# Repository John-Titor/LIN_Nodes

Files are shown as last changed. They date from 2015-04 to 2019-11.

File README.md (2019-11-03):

Firmware and PCB designs for various LIN network nodes intended for retrofitting older vehicles.

```
boards/
    Eagle schematic and PCB files.

common/
    Protocol definitions and generator.

Documentation/
    Datasheets for various parts used in the design.

lintool
    Host-side configuration tool. Talks to the usb_link hardware.

nodes/
    All of the nodes in this part of the tree are based on the Atmel ATTiny167.

    bl_core/
        LIN bootloader core, consumed by bl_installer.

    bl_installer/
        Bootloader installer; flashed onto a fresh board this will install the
        bootloader.

        The installed bootloader comes up on NAD 32 and can be flashed with lintool
        by explicitly supplying the node address and firmware file.

        lintool update -n 32 <path-to-fw-file>

        Only one node can be in this 'recovery' mode on the network when doing this.

    lib/
        Shared code.

    master/
        Network master node. Supports 7 switch-to-battery and 14 switch-to-ground
        inputs. 4 of the switch-to-ground inputs can also be 0-5V voltage inputs,
        with optional 2 or 16mA current sources for measuring resistive sensors.

    power_v3/
        5-output power switching node using Freescale smart high-side switches.
        Board limited to 5.5A, but code should work with the 10A device as well.
        Outputs support PWM, current monitoring, open- and short-circuit detection,
        overcurrent and overtemperature protection, etc.

    usb_link/
        USB bridge with support for configuration and node firmware updates.

```

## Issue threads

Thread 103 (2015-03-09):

define test hardware configuration

John-Titor, 2015-03-09:
Probably:

 - USB link
 - master connected to Phidget relay board
 - slave connected to Phidget control board, also current & voltage sensor connected
 - 12V power supply on bus

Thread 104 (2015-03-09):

build test framework

John-Titor, 2015-03-09:
Subtask of #29

Framework should support at least:

- Initialise and check for all required hardware
- Utility functions for generating, loading, verifying node configuration
- Utility functions for measuring voltage, current, signal state
- Utility functions for controlling relays
- Complex checking functions (check for blinking, measure duty cycle, capture one-shot behaviours)
- Simple tests for verifying the correct configuration of the test hardware setup
- Logging
- Test runner

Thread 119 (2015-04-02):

param ... -d option does not work as documented

John-Titor, 2015-04-02:
It claims to print the default value, but instead it will cause the value to be set to its default.

Need to work out which is correct...

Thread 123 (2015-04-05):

turn marker lights off after timeout

John-Titor, 2015-04-05:
In order to avoid running the battery down, we should turn off the marker lights after a reasonable period

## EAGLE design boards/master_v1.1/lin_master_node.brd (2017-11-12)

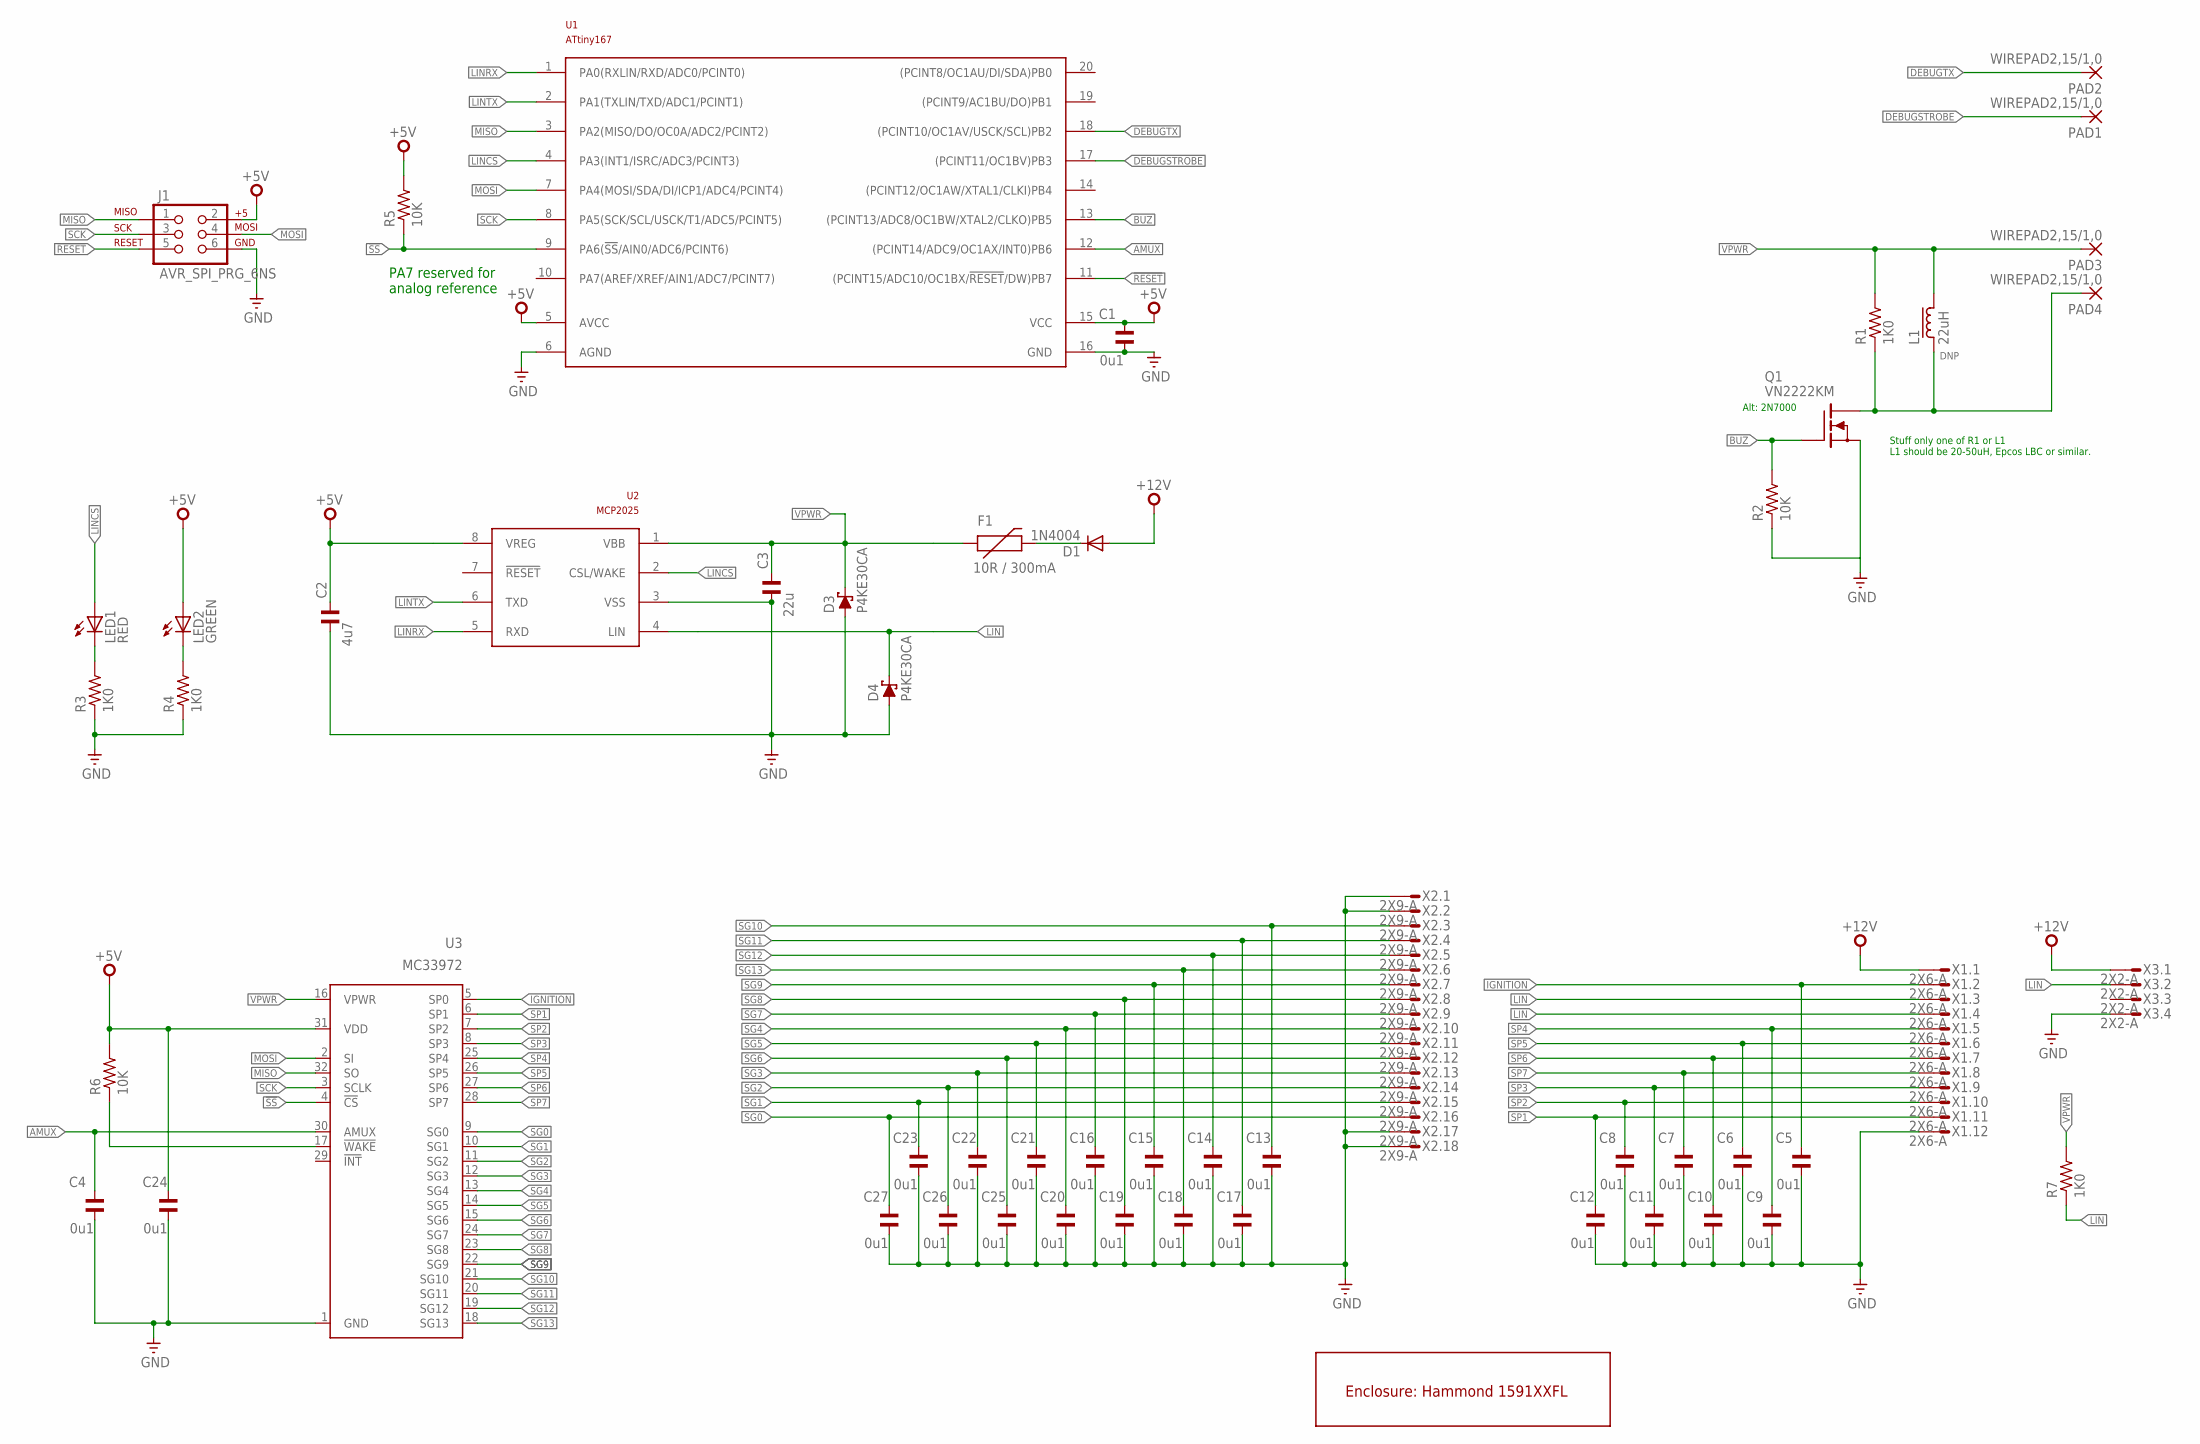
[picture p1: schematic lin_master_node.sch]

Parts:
C1, C4, C24: 0u1; C050-024X044; PARTNO FK28X7R1H104K
C2: 4u7; C050-024X044; PARTNO FK28X5R0J475K
C3: 22u; C050-024X044; PARTNO FK22X5R1E226M
C5, C6, C7, C8, C9, C10, C11, C12, C13, C14, C15, C16, C17, C18, C19, C20, C21, C22, C23, C25, C26, C27: 0u1; C0805K; PARTNO C2012X7R1H104K085AA
D1: 1N4004; DO41-10; PARTNO 1N4004-TP
D3, D4: P4KE30CA; DO41-10; PARTNO P4KE30CA
F1: 10R / 300mA; PTC; PARTNO CMF-RL10-0
J1: AVR_SPI_PRG_6NS; 2X3-NS
L1: 22uH; LBC15A
LED1: RED; LED3MM; PARTNO C4SMF-RJS-CT0W0BB2
LED2: GREEN; LED3MM; PARTNO C4SMF-GJS-CV0Y0792
PAD1, PAD2, PAD3, PAD4: WIREPAD2,15/1,0; 2,15/1,0
Q1: VN2222KM; TO237
R1, R3, R4, R7: 1K0; 0207/10; PARTNO CF14JT1K00
R2, R5, R6: 10K; 0207/10; PARTNO CF14JT10K0
U1: ATtiny167; SO20W; PARTNO ATTINY167-SU
U2: MCP2025; SO08; PARTNO MCP2025-500E/SN
U3: MC33972; SOIC32W; PARTNO MC33972ATEW
U$1: 1591XXAFL; PARTNO 1591XXAFLBK
X1: 2X6-A; 4-794618-2; PARTNO 4-794618-2
X2: 2X9-A; 4-794618-8; PARTNO 4-794618-8
X3: 2X2-A; 3-794618-4; PARTNO 3-794618-4

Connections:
!RESET: J1.5, U1.11 ((PCINT15/ADC10/OC1BX/!RESET!/DW)PB7)
!SS: R5.1, U1.9 (PA6(!SS!/AIN0/ADC6/PCINT6)), U3.4 (!CS)
+5V: C1.1, C2.1, C24.1, J1.2, LED2.A, R5.2, R6.2, U1.5 (AVCC), U1.15 (VCC), U2.8 (VREG), U3.31 (VDD)
+12V: D1.A, X1.1, X3.1
AMUX: C4.1, U1.12 ((PCINT14/ADC9/OC1AX/INT0)PB6), U3.30 (AMUX)
BUZ: Q1.2 (G), R2.2, U1.13 ((PCINT13/ADC8/OC1BW/XTAL2/CLKO)PB5)
DEBUGSTROBE: PAD1.1, U1.17 ((PCINT11/OC1BV)PB3)
DEBUGTX: PAD2.1, U1.18 ((PCINT10/OC1AV/USCK/SCL)PB2)
GND: C1.2, C2.2, C3.2, C4.2, C5.2, C6.2, C7.2, C8.2, C9.2, C10.2, C11.2, C12.2, C13.2, C14.2, C15.2, C16.2, C17.2, C18.2, C19.2, C20.2, C21.2, C22.2, C23.2, C24.2, C25.2, C26.2, C27.2, D3.A, D4.A, J1.6, Q1.3 (S), R2.1, R3.1, R4.1, U1.6 (AGND), U1.16 (GND), U2.3 (VSS), U3.1 (GND), X1.12, X2.1, X2.2, X2.17, X2.18, X3.4
IGNITION: C5.1, U3.5 (SP0), X1.2
LIN: D4.C, R7.1, U2.4 (LIN), X1.3, X1.4, X3.2
LINCS: LED1.A, U1.4 (PA3(INT1/ISRC/ADC3/PCINT3)), U2.2 (CSL/WAKE)
LINRX: U1.1 (PA0(RXLIN/RXD/ADC0/PCINT0)), U2.5 (RXD)
LINTX: U1.2 (PA1(TXLIN/TXD/ADC1/PCINT1)), U2.6 (TXD)
MISO: J1.1, U1.3 (PA2(MISO/DO/OC0A/ADC2/PCINT2)), U3.32 (SO)
MOSI: J1.4, U1.7 (PA4(MOSI/SDA/DI/ICP1/ADC4/PCINT4)), U3.2 (SI)
unnamed: LED1.K (C), R3.2
unnamed: R6.1, U3.17 (!WAKE)
unnamed: L1.1, PAD4.1, Q1.1 (D), R1.1
unnamed: LED2.K (C), R4.2
unnamed: D1.C, F1.P$2 (2)
SCK: J1.3, U1.8 (PA5(SCK/SCL/USCK/T1/ADC5/PCINT5)), U3.3 (SCLK)
SG0: C27.1, U3.9 (SG0), X2.16
SG1: C23.1, U3.10 (SG1), X2.15
SG2: C26.1, U3.11 (SG2), X2.14
SG3: C22.1, U3.12 (SG3), X2.13
SG4: C20.1, U3.13 (SG4), X2.10
SG5: C21.1, U3.14 (SG5), X2.11
SG6: C25.1, U3.15 (SG6), X2.12
SG7: C16.1, U3.24 (SG7), X2.9
SG8: C19.1, U3.23 (SG8), X2.8
SG9: C15.1, U3.22 (SG9), X2.7
SG10: C13.1, U3.21 (SG10), X2.3
SG11: C17.1, U3.20 (SG11), X2.4
SG12: C14.1, U3.19 (SG12), X2.5
SG13: C18.1, U3.18 (SG13), X2.6
SP1: C12.1, U3.6 (SP1), X1.11
SP2: C8.1, U3.7 (SP2), X1.10
SP3: C11.1, U3.8 (SP3), X1.9
SP4: C9.1, U3.25 (SP4), X1.5
SP5: C6.1, U3.26 (SP5), X1.6
SP6: C10.1, U3.27 (SP6), X1.7
SP7: C7.1, U3.28 (SP7), X1.8
VPWR: C3.1, D3.C, F1.P$1 (1), L1.2, PAD3.1, R1.2, R7.2, U2.1 (VBB), U3.16 (VPWR)

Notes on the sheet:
PA7 reserved for analog reference
Stuff only one of R1 or L1 L1 should be 20-50uH, Epcos LBC or similar.
Alt: 2N7000

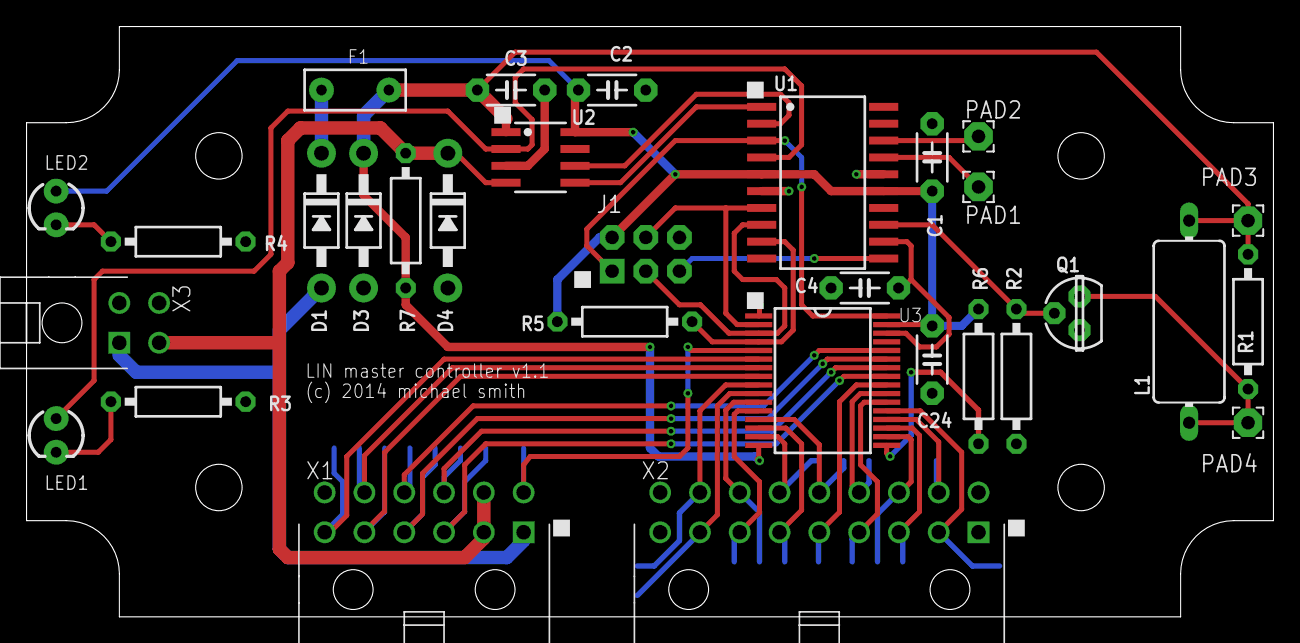
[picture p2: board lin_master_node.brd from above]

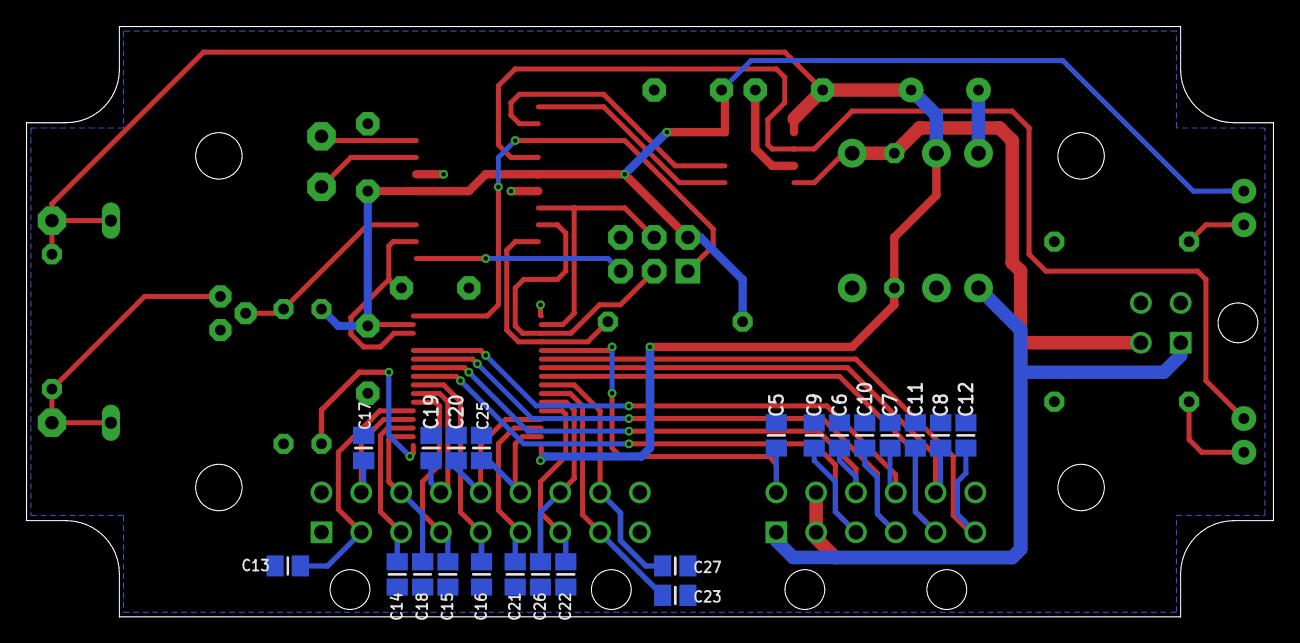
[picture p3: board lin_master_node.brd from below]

Board: 2 copper layers, 94.0 x 44.5 mm, 54 parts (22 on the bottom side), 44 nets.

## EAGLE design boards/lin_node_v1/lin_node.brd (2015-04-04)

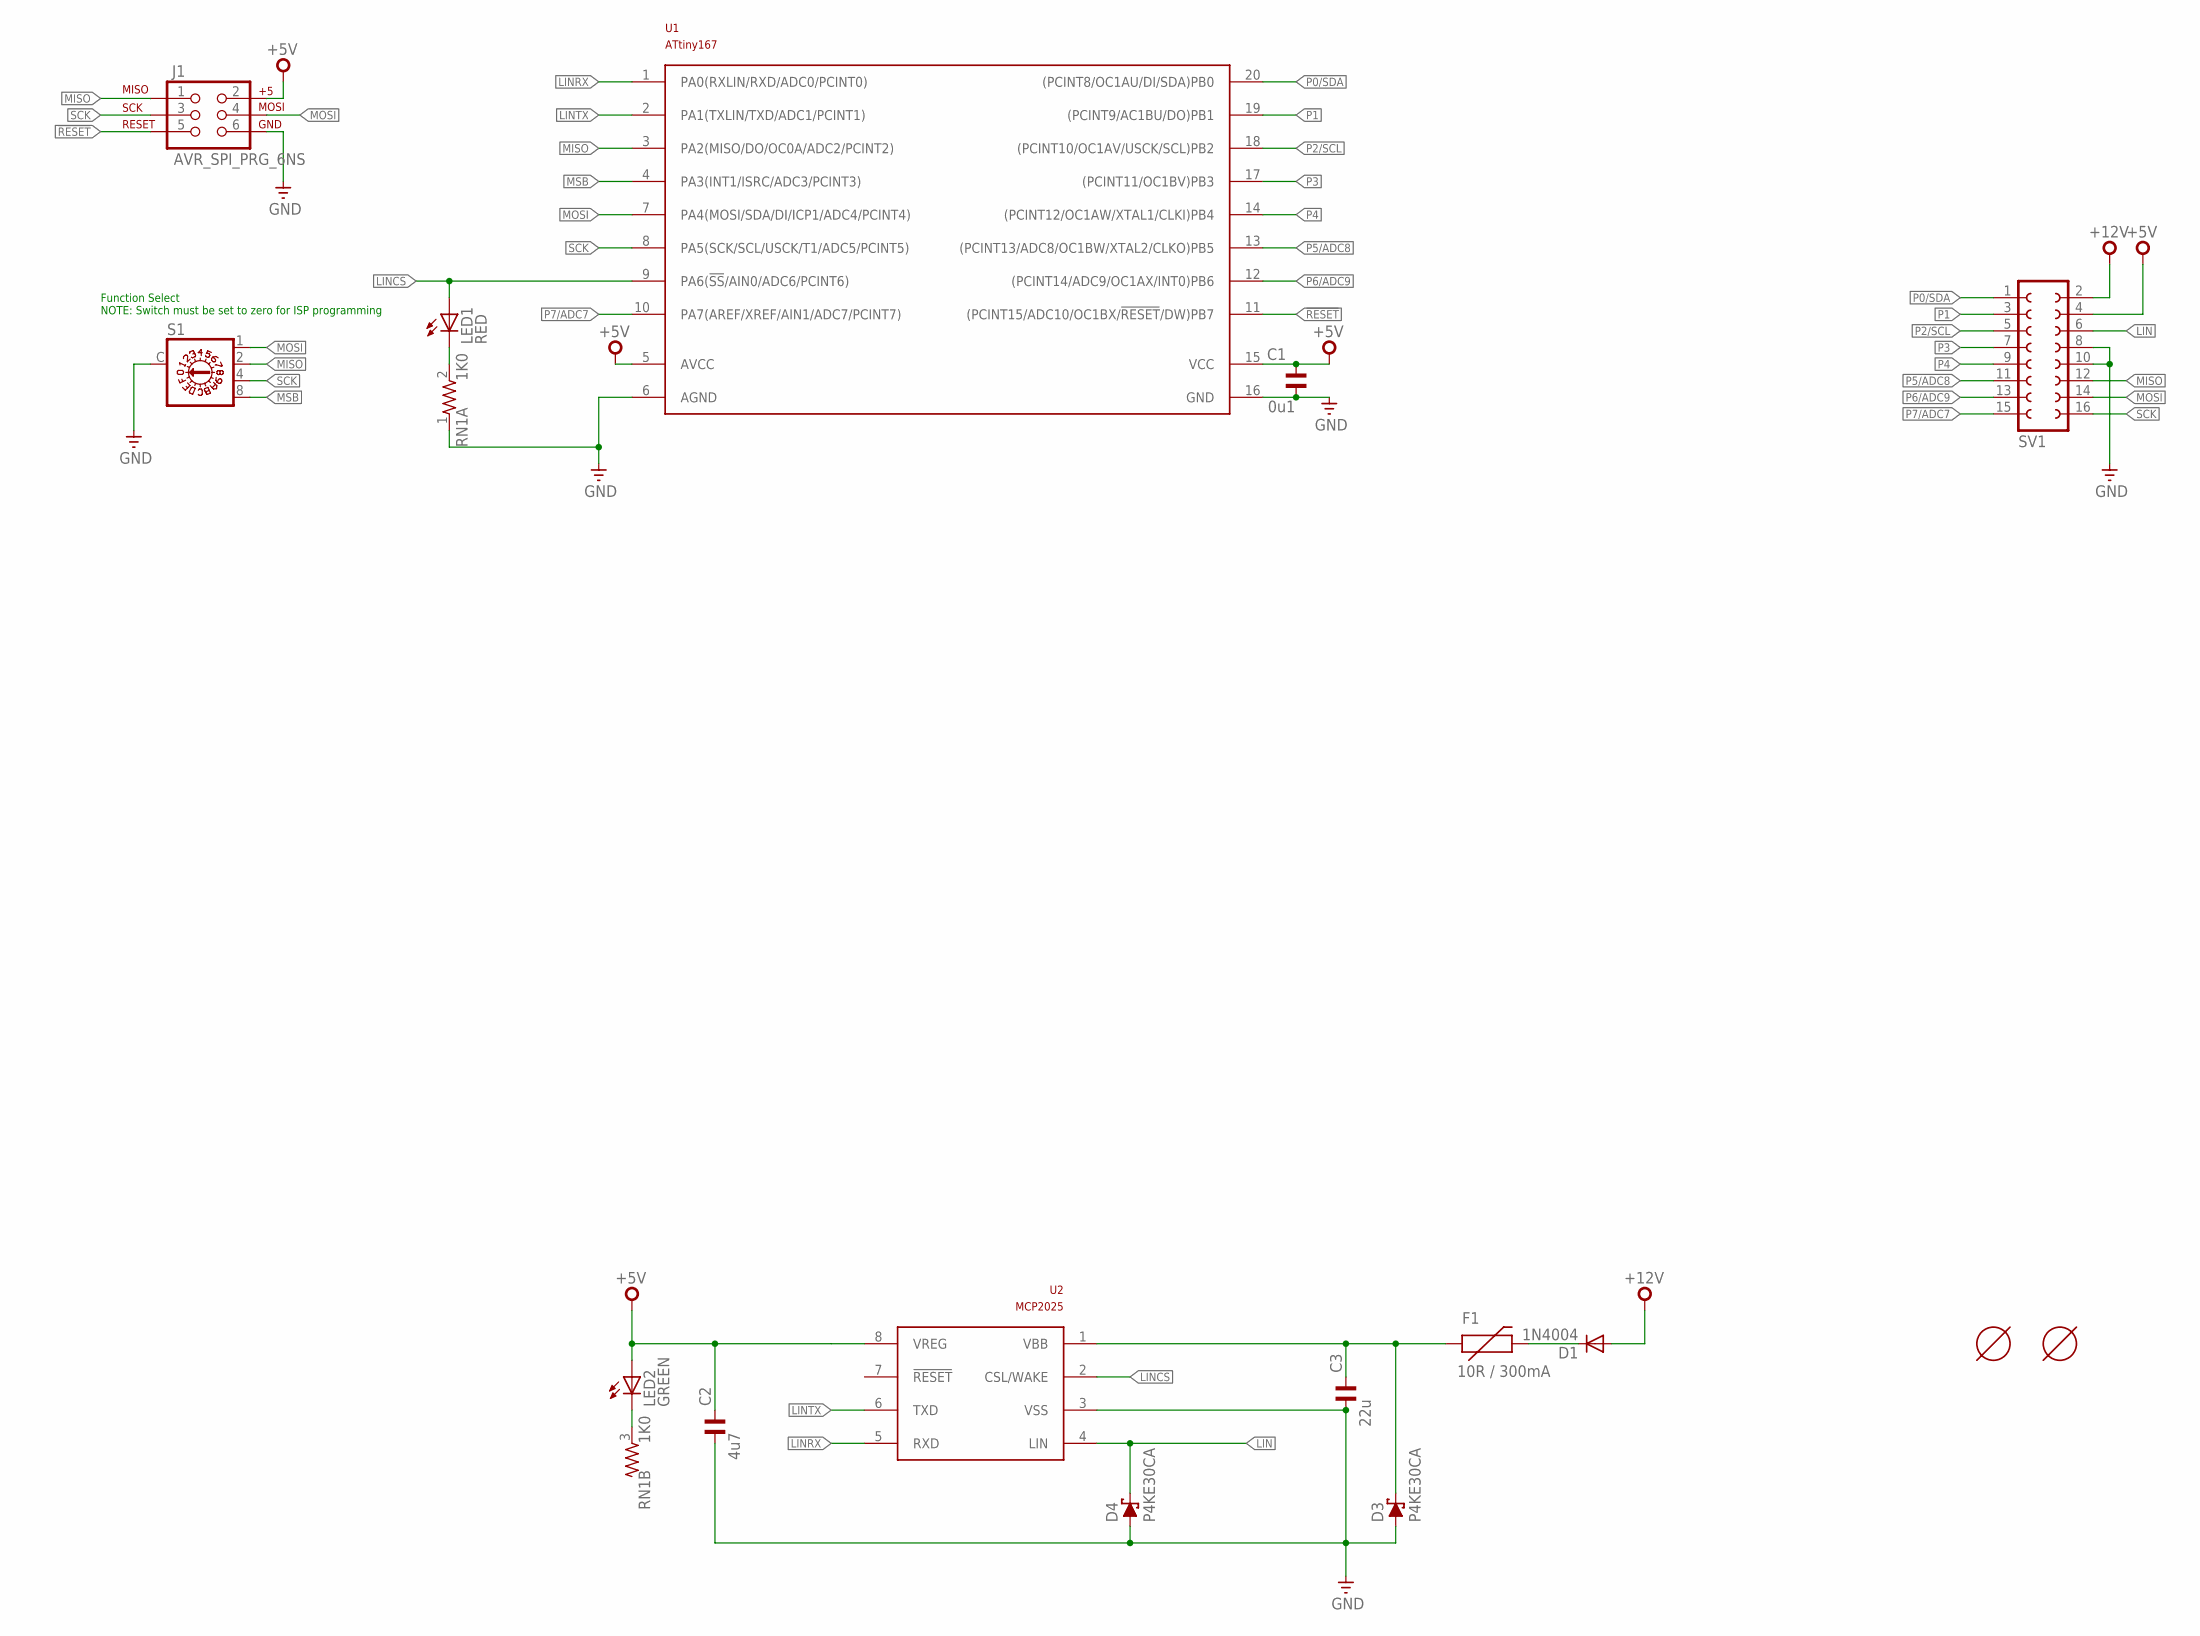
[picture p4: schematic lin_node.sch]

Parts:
C1: 0u1; C025-024X044; PARTNO FK28X7R1H104K
C2: 4u7; C050-024X044; PARTNO FK28X5R0J475K
C3: 22u; C050-024X044; PARTNO FK22X5R1E226M
D1: 1N4004; DO41-10; PARTNO 1N4004-TP
D3, D4: P4KE30CA; DO41-10; PARTNO P4KE30CA
F1: 10R / 300mA; PTC; PARTNO 600R150-RBZR
J1: AVR_SPI_PRG_6NS; 2X3-NS
LED1: RED; LED3MM; PARTNO C4SMF-RJS-CT0W0BB2
LED2: GREEN; LED3MM; PARTNO C4SMF-GJS-CV0Y0792
RN1: 1K0; SIL4; PARTNO 4604X-101-103LF
S1: P103; PARTNO SH-7050MC
SV1: FE08-2
U1: ATtiny167; SO20W; PARTNO ATTINY167-SU
U2: MCP2025; SO08; PARTNO MCP2025-500E/SN
U$1, U$2: MOUNT-HOLE3.1MM; MOUNT-HOLE3.1

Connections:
!RESET: J1.5, U1.11 ((PCINT15/ADC10/OC1BX/!RESET!/DW)PB7)
+5V: C1.1, C2.1, J1.2, LED2.A, SV1.4, U1.5 (AVCC), U1.15 (VCC), U2.8 (VREG)
+12V: D1.A, SV1.2
GND: C1.2, C2.2, C3.2, D3.A, D4.A, J1.6, RN1.1, S1.C, SV1.8, SV1.10, U1.6 (AGND), U1.16 (GND), U2.3 (VSS)
LIN: D4.C, SV1.6, U2.4 (LIN)
LINCS: LED1.A, U1.9 (PA6(!SS!/AIN0/ADC6/PCINT6)), U2.2 (CSL/WAKE)
LINRX: U1.1 (PA0(RXLIN/RXD/ADC0/PCINT0)), U2.5 (RXD)
LINTX: U1.2 (PA1(TXLIN/TXD/ADC1/PCINT1)), U2.6 (TXD)
MISO: J1.1, S1.2, SV1.12, U1.3 (PA2(MISO/DO/OC0A/ADC2/PCINT2))
MOSI: J1.4, S1.1, SV1.14, U1.7 (PA4(MOSI/SDA/DI/ICP1/ADC4/PCINT4))
MSB: S1.8, U1.4 (PA3(INT1/ISRC/ADC3/PCINT3))
unnamed: C3.1, D3.C, F1.P$1 (1), U2.1 (VBB)
unnamed: LED1.K (C), RN1.2
unnamed: LED2.K (C), RN1.3 (2)
unnamed: D1.C, F1.P$2 (2)
P0/SDA: SV1.1, U1.20 ((PCINT8/OC1AU/DI/SDA)PB0)
P1: SV1.3, U1.19 ((PCINT9/AC1BU/DO)PB1)
P2/SCL: SV1.5, U1.18 ((PCINT10/OC1AV/USCK/SCL)PB2)
P3: SV1.7, U1.17 ((PCINT11/OC1BV)PB3)
P4: SV1.9, U1.14 ((PCINT12/OC1AW/XTAL1/CLKI)PB4)
P5/ADC8: SV1.11, U1.13 ((PCINT13/ADC8/OC1BW/XTAL2/CLKO)PB5)
P6/ADC9: SV1.13, U1.12 ((PCINT14/ADC9/OC1AX/INT0)PB6)
P7/ADC7: SV1.15, U1.10 (PA7(AREF/XREF/AIN1/ADC7/PCINT7))
SCK: J1.3, S1.4, SV1.16, U1.8 (PA5(SCK/SCL/USCK/T1/ADC5/PCINT5))

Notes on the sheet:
Function Select NOTE: Switch must be set to zero for ISP programming

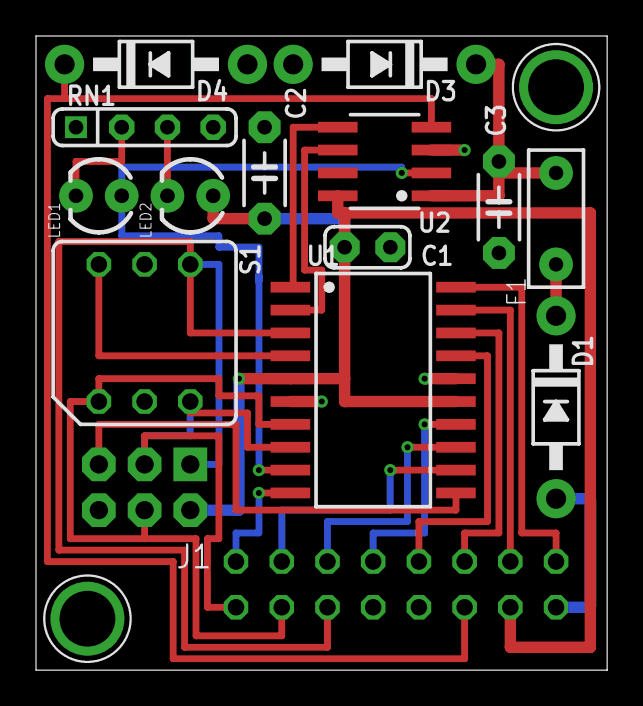
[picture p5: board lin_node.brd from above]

Board: 2 copper layers, 31.7 x 35.2 mm, 17 parts (1 on the bottom side), 24 nets.

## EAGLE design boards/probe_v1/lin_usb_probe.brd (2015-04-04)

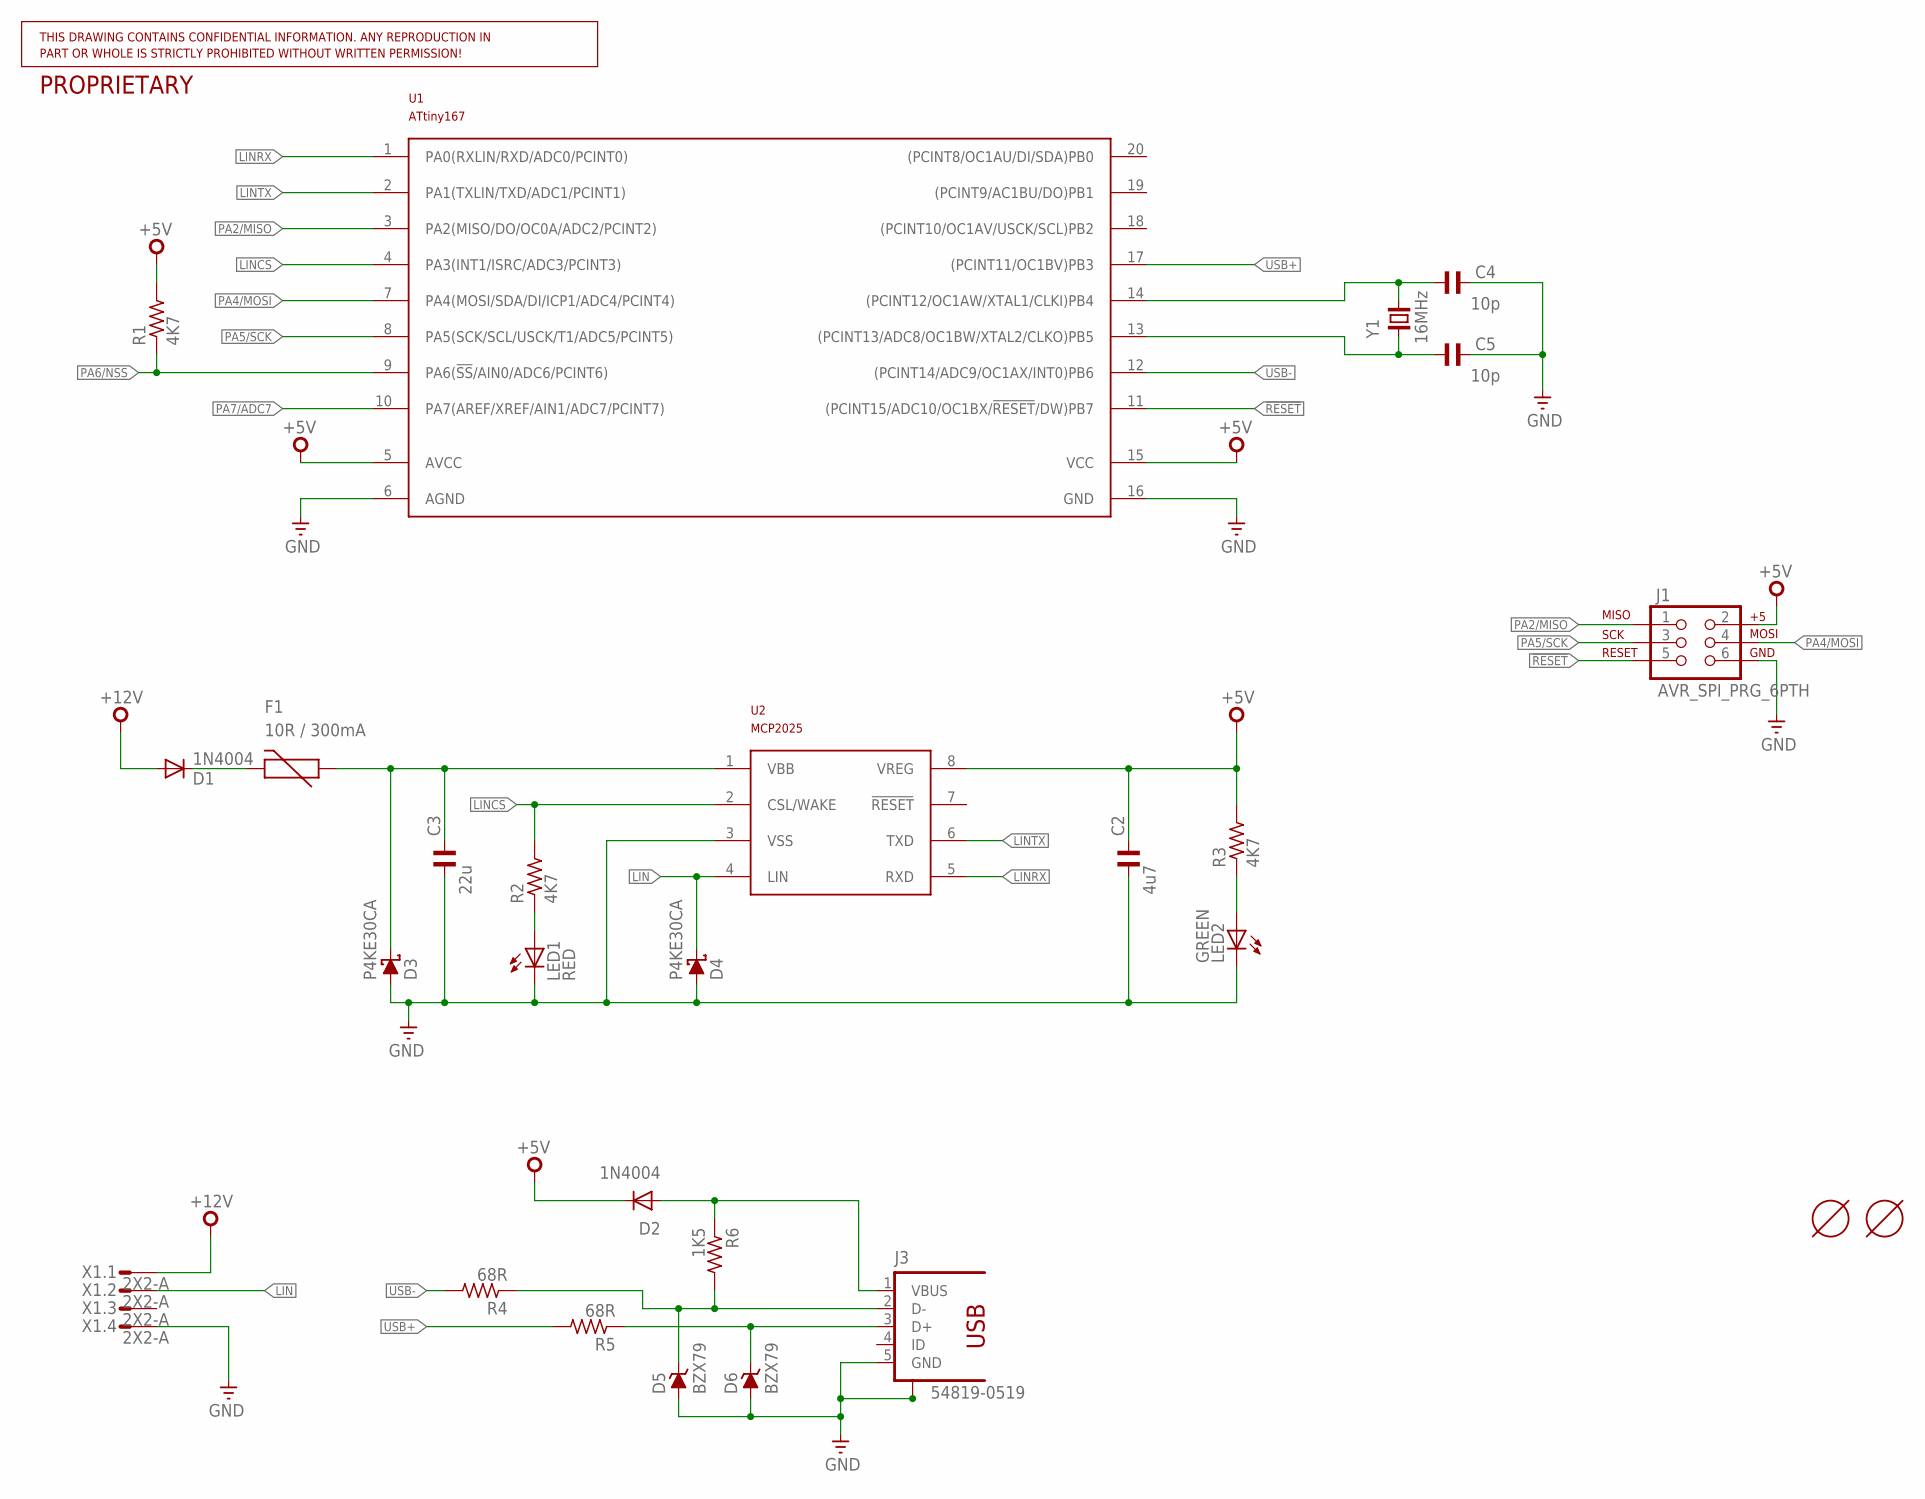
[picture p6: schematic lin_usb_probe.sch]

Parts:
C2: 4u7; C050-024X044; PARTNO GRM21BR71A475KA73K
C3: 22u; C050-024X044; PARTNO C2012X5R1V226M125AC
C4, C5: 10p; C025-024X044
D1: 1N4004; DO41-10; PARTNO 1N4004-TP
D2: 1N4004; DO41-10
D3, D4: P4KE30CA; DO41-10; PARTNO P4KE30CA
D5, D6: BZX79; DO35Z10
F1: 10R / 300mA; PTC; PARTNO 600R150-RBZR
J1: AVR_SPI_PRG_6PTH; 2X3
J3: 54819-0519
LED1: RED; LED3MM; PARTNO C4SMF-RJS-CT0W0BB2
LED2: GREEN; LED3MM; PARTNO C4SMF-GJS-CV0Y0792
R1, R2, R3: 4K7; 0207/10; PARTNO ERJ-6GEYJ472V
R4, R5: 68R; 0207/10; PARTNO ERJ-6GEYJ472V
R6: 1K5; 0207/10; PARTNO ERJ-6GEYJ472V
U1: ATtiny167; TSSOP20; PARTNO ATTINY167-A15XZ
U2: MCP2025; SO08; PARTNO MCP2025-500E/SN
U$1, U$2: MOUNT-HOLE3.1MM; MOUNT-HOLE3.1
X1: 2X2-A; 3-794618-4
Y1: 16MHz; HC49/S

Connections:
!RESET: J1.5, U1.11 ((PCINT15/ADC10/OC1BX/!RESET!/DW)PB7)
+5V: C2.1, D2.C, J1.2, R1.2, R3.2, U1.5 (AVCC), U1.15 (VCC), U2.8 (VREG)
+12V: D1.A, X1.1
GND: C2.2, C3.2, C4.1, C5.1, D3.A, D4.A, D5.A, D6.A, J1.6, J3.5 (GND), J3.S1, J3.S2, LED1.K (C), LED2.K (C), U1.6 (AGND), U1.16 (GND), U2.3 (VSS), X1.4
LIN: D4.C, U2.4 (LIN), X1.2
LINCS: R2.2, U1.4 (PA3(INT1/ISRC/ADC3/PCINT3)), U2.2 (CSL/WAKE)
LINRX: U1.1 (PA0(RXLIN/RXD/ADC0/PCINT0)), U2.5 (RXD)
LINTX: U1.2 (PA1(TXLIN/TXD/ADC1/PCINT1)), U2.6 (TXD)
unnamed: C4.2, U1.14 ((PCINT12/OC1AW/XTAL1/CLKI)PB4), Y1.2
unnamed: C3.1, D3.C, F1.P$1 (1), U2.1 (VBB)
unnamed: LED1.A, R2.1
unnamed: LED2.A, R3.1
unnamed: D1.C, F1.P$2 (2)
unnamed: D6.C, J3.3 (D+), R5.1
unnamed: D5.C, J3.2 (D-), R4.1, R6.2
unnamed: D2.A, J3.1 (VBUS), R6.1
unnamed: C5.2, U1.13 ((PCINT13/ADC8/OC1BW/XTAL2/CLKO)PB5), Y1.1
PA2/MISO: J1.1, U1.3 (PA2(MISO/DO/OC0A/ADC2/PCINT2))
PA4/MOSI: J1.4, U1.7 (PA4(MOSI/SDA/DI/ICP1/ADC4/PCINT4))
PA5/SCK: J1.3, U1.8 (PA5(SCK/SCL/USCK/T1/ADC5/PCINT5))
PA6/NSS: R1.1, U1.9 (PA6(!SS!/AIN0/ADC6/PCINT6))
PA7/ADC7: U1.10 (PA7(AREF/XREF/AIN1/ADC7/PCINT7))
USB+: R5.2, U1.17 ((PCINT11/OC1BV)PB3)
USB-: R4.2, U1.12 ((PCINT14/ADC9/OC1AX/INT0)PB6)

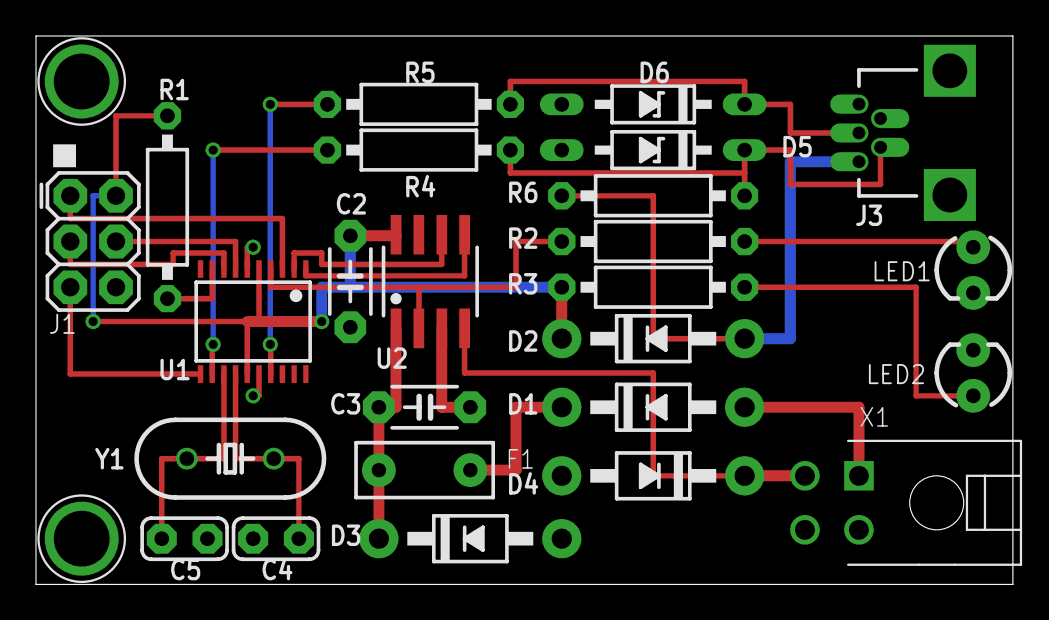
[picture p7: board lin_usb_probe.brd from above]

Board: 2 copper layers, 54.3 x 30.5 mm, 27 parts (0 on the bottom side), 23 nets.

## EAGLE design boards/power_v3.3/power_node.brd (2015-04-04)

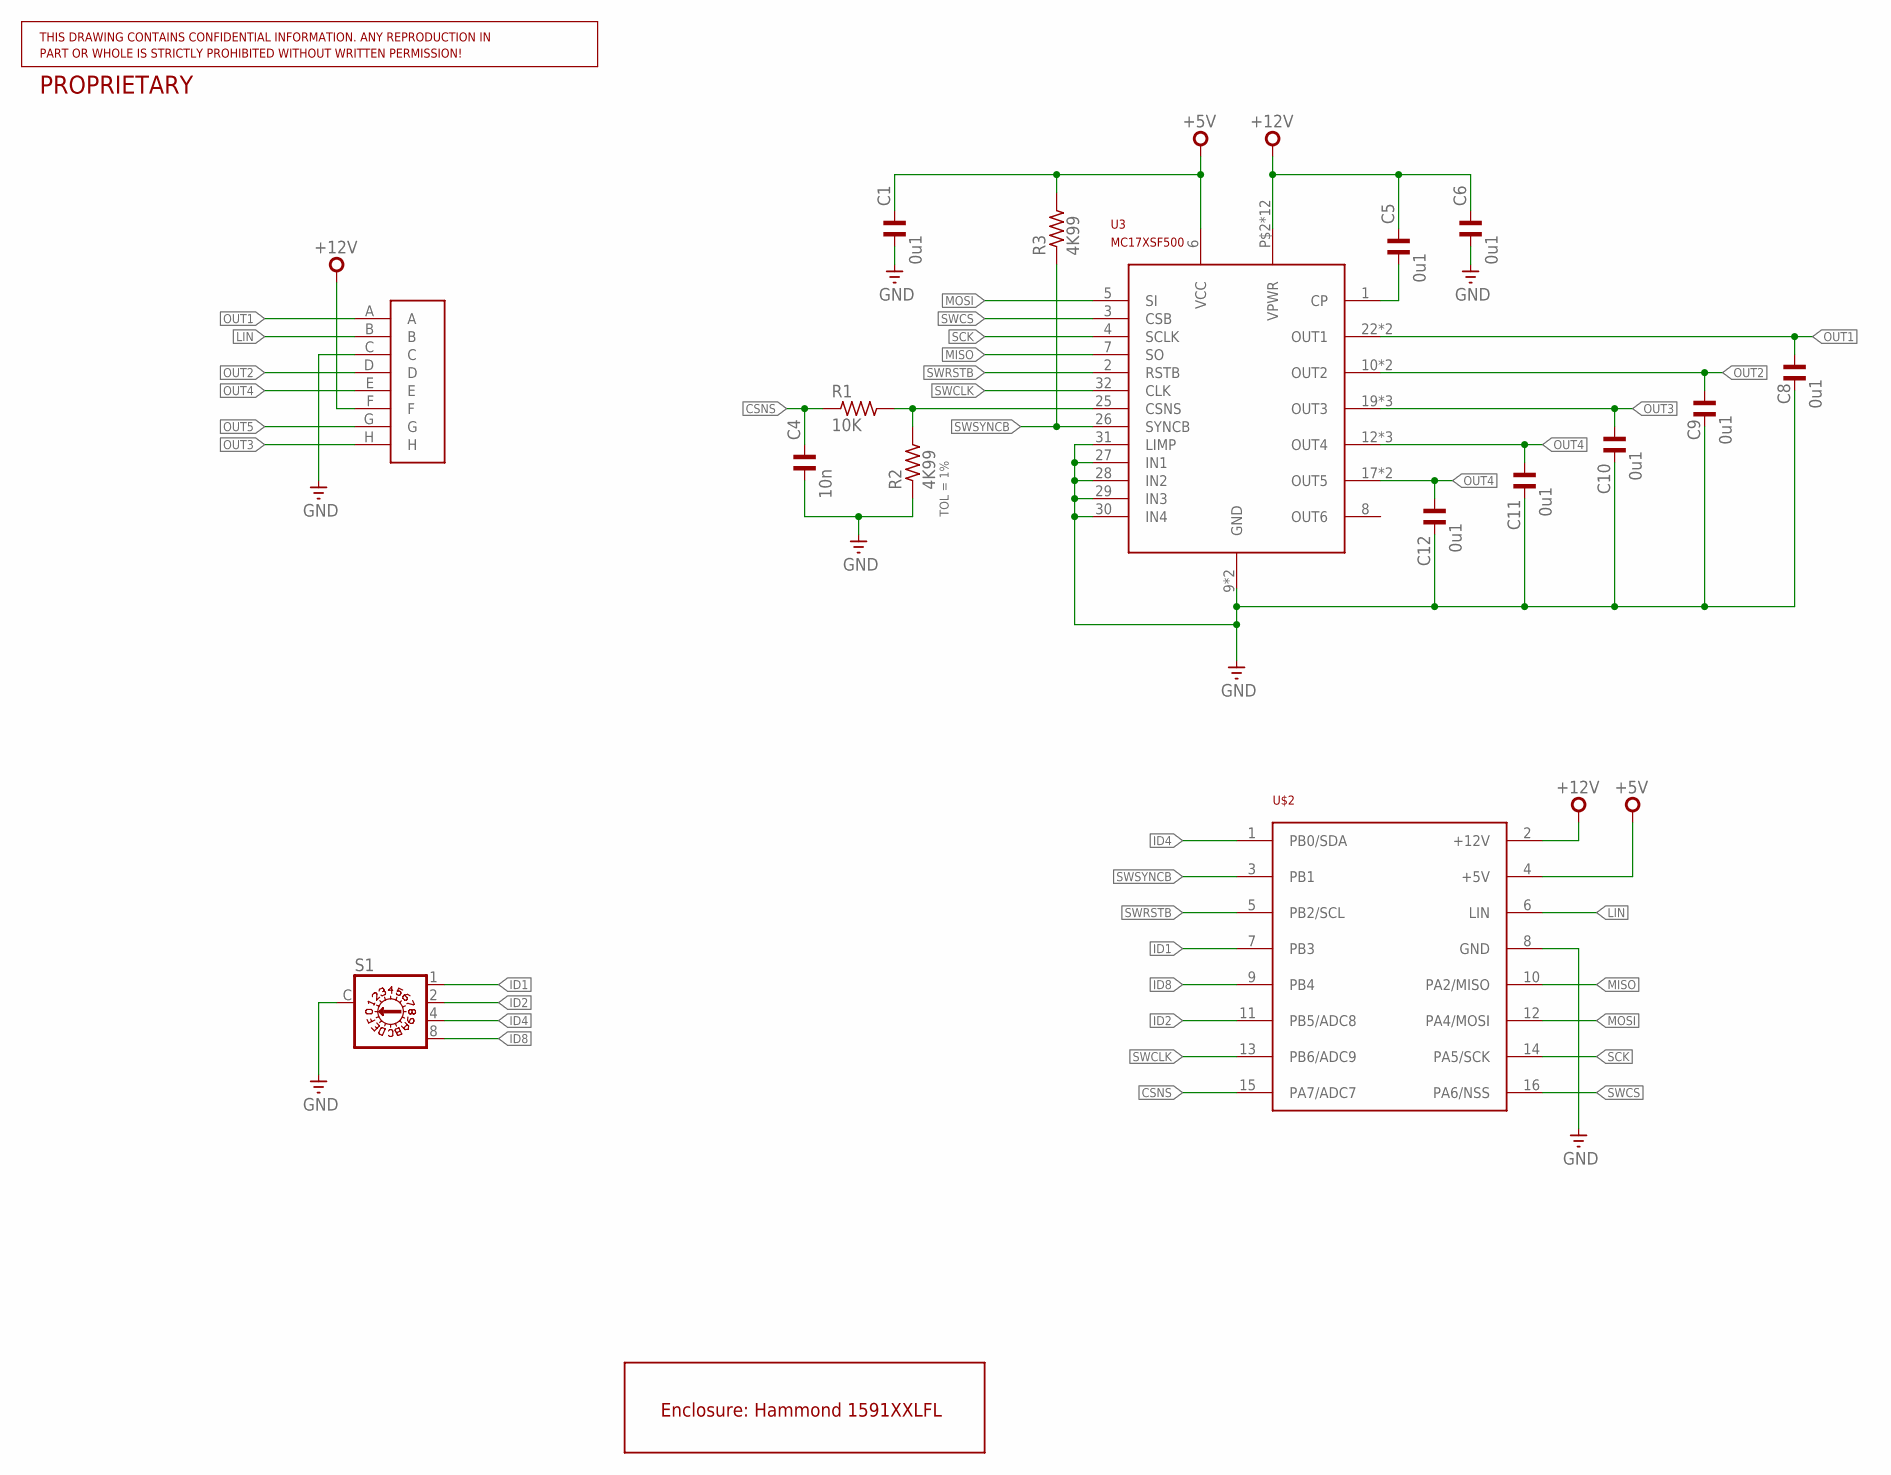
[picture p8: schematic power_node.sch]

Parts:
C1, C5, C6: 0u1; C0805K; PARTNO FK28X7R1H104K
C4: 10n; C0805K; PARTNO FK18X7R1H103K
C8, C9, C10, C11, C12: 0u1; C0805K; PARTNO C1608X7R1H104M080AA
J2: 12146734; PARTNO 12146724-B
R1: 10K; R0805W; PARTNO CF14JT10K0
R2, R3: 4K99; R0805W; PARTNO MFR-25FBF52-4K99
S1: P103; PARTNO SH-7050MC
U3: MC17XSF500; SOIC32W-EP; PARTNO MC17XSF500EK
U$1: 1591XXLFL; PARTNO 1591XXLFLBK
U$2: LIN_NODEHORIZ; LIN_NODE

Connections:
+5V: C1.1, R3.2, U3.6 (VCC), U$2.4 (+5V)
+12V: C5.1, C6.1, J2.F, U3.P$2 (VPWR), U3.P$3 (VPWR), U3.P$4 (VPWR), U3.P$5 (VPWR), U3.P$6 (VPWR), U3.P$7 (VPWR), U3.P$8 (VPWR), U3.P$9 (VPWR), U3.P$10 (VPWR), U3.P$11 (VPWR), U3.P$12 (VPWR), U3.P$13 (VPWR), U$2.2 (+12V)
CSNS: C4.1, R1.1, U$2.15 (PA7/ADC7)
GND: C1.2, C4.2, C6.2, C8.2, C9.2, C10.2, C11.2, C12.2, J2.C, R2.1, S1.C, U3.9 (GND), U3.24 (GND), U3.27 (IN1), U3.28 (IN2), U3.29 (IN3), U3.30 (IN4), U3.31 (LIMP), U$2.8 (GND)
ID1: S1.1, U$2.7 (PB3)
ID2: S1.2, U$2.11 (PB5/ADC8)
ID4: S1.4, U$2.1 (PB0/SDA)
ID8: S1.8, U$2.9 (PB4)
LIN: J2.B, U$2.6 (LIN)
MISO: U3.7 (SO), U$2.10 (PA2/MISO)
MOSI: U3.5 (SI), U$2.12 (PA4/MOSI)
unnamed: C5.2, U3.1 (CP)
unnamed: R1.2, R2.2, U3.25 (CSNS)
OUT1: C8.1, J2.A, U3.22 (OUT1), U3.23 (OUT1)
OUT2: C9.1, J2.D, U3.10 (OUT2), U3.11 (OUT2)
OUT3: C10.1, J2.H, U3.19 (OUT3), U3.20 (OUT3), U3.21 (OUT3)
OUT4: C11.1, J2.E, U3.12 (OUT4), U3.13 (OUT4), U3.14 (OUT4)
OUT5: C12.1, J2.G, U3.17 (OUT5), U3.18 (OUT5)
SCK: U3.4 (SCLK), U$2.14 (PA5/SCK)
SWCLK: U3.32 (CLK), U$2.13 (PB6/ADC9)
SWCS: U3.3 (CSB), U$2.16 (PA6/NSS)
SWRSTB: U3.2 (RSTB), U$2.5 (PB2/SCL)
SWSYNCB: R3.1, U3.26 (SYNCB), U$2.3 (PB1)

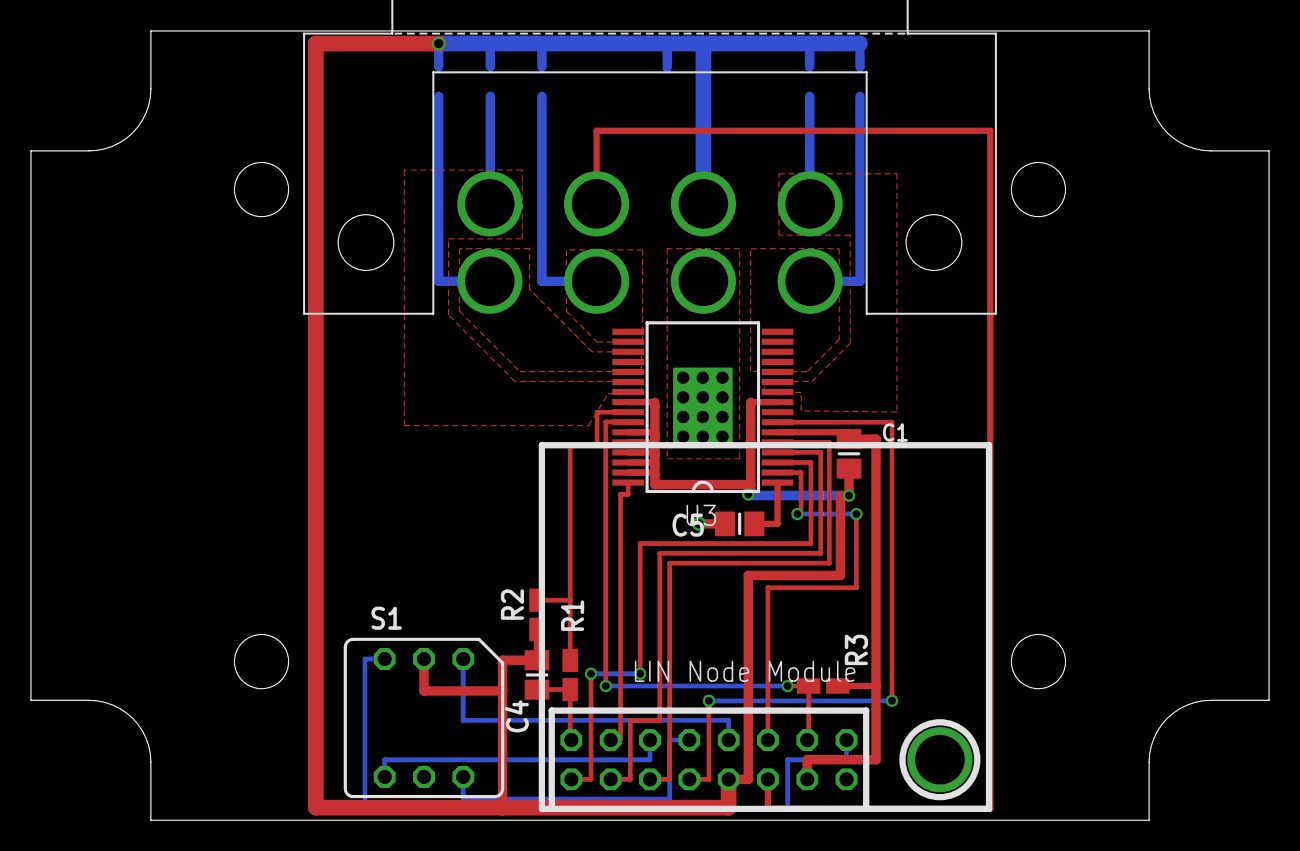
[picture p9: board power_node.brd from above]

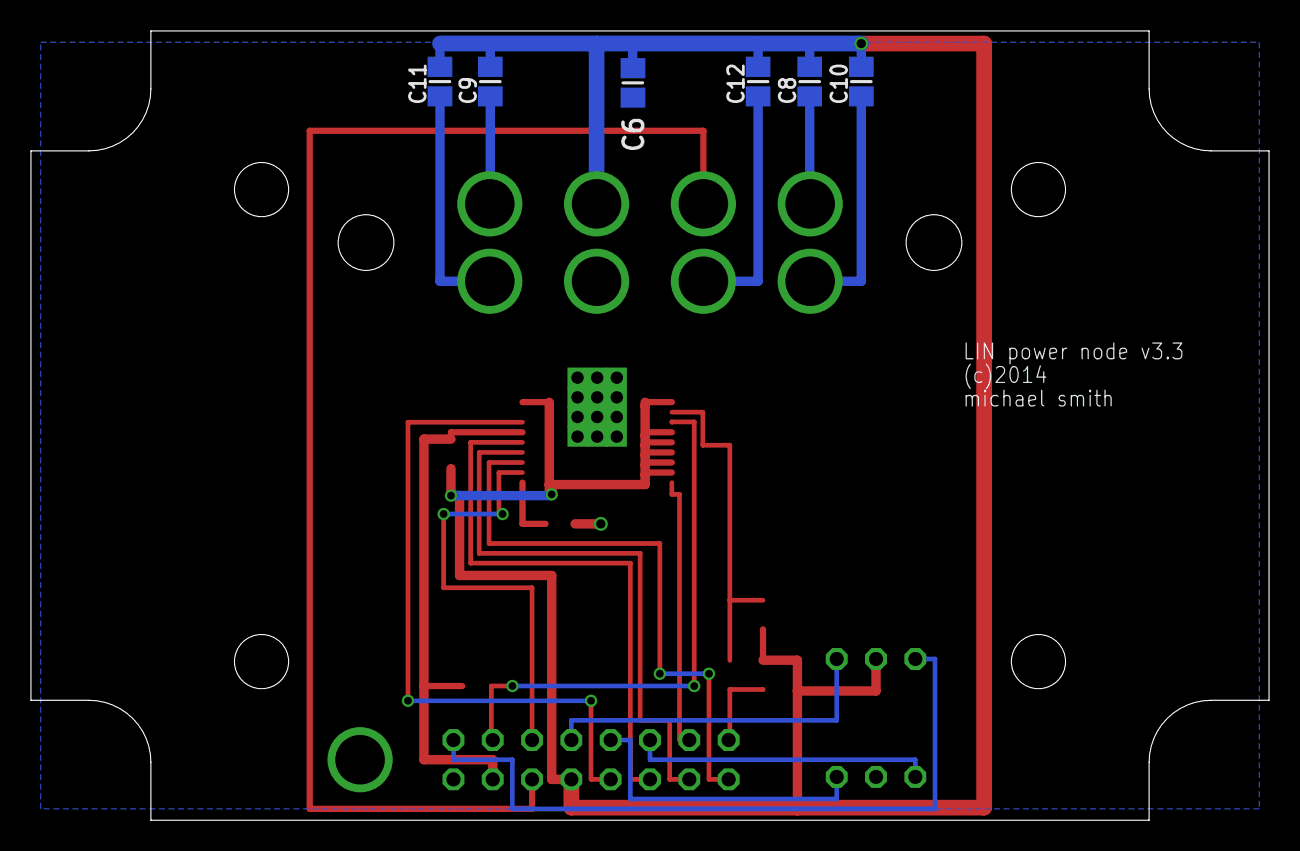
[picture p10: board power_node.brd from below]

Board: 2 copper layers, 80.0 x 51.0 mm, 17 parts (6 on the bottom side), 23 nets.

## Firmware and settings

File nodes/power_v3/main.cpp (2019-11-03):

/*
 * Copyright (c) 2012-2015, Mike Smith, <msmith@purgatory.org>
 * All rights reserved.
 *
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
 * o Redistributions in binary form must reproduce the above copyright
 *   notice, this list of conditions and the following disclaimer in the
 *   documentation and/or other materials provided with the distribution.
 *
 * THIS SOFTWARE IS PROVIDED BY THE COPYRIGHT HOLDERS AND CONTRIBUTORS
 * "AS IS" AND ANY EXPRESS OR IMPLIED WARRANTIES, INCLUDING, BUT NOT
 * LIMITED TO, THE IMPLIED WARRANTIES OF MERCHANTABILITY AND FITNESS FOR
 * A PARTICULAR PURPOSE ARE DISCLAIMED. IN NO EVENT SHALL THE COPYRIGHT
 * HOLDER OR CONTRIBUTORS BE LIABLE FOR ANY DIRECT, INDIRECT, INCIDENTAL,
 * SPECIAL, EXEMPLARY, OR CONSEQUENTIAL DAMAGES (INCLUDING, BUT NOT
 * LIMITED TO, PROCUREMENT OF SUBSTITUTE GOODS OR SERVICES; LOSS OF USE,
 * DATA, OR PROFITS; OR BUSINESS INTERRUPTION) HOWEVER CAUSED AND ON ANY
 * THEORY OF LIABILITY, WHETHER IN CONTRACT, STRICT LIABILITY, OR TORT
 * (INCLUDING NEGLIGENCE OR OTHERWISE) ARISING IN ANY WAY OUT OF THE USE
 * OF THIS SOFTWARE, EVEN IF ADVISED OF THE POSSIBILITY OF SUCH DAMAGE.
 */

#include <avr/wdt.h>
#include <avr/interrupt.h>
#include <avr/eeprom.h>

#include "board.h"
#include "slave.h"
#include "mc17xsf500.h"

#include "lin_defs.h"

static uint8_t node_status;
static uint8_t output_status[MC17XSF500::num_channels];
static uint16_t current[MC17XSF500::num_channels];
static uint16_t info[8];
static uint16_t free_memory;

using namespace PowerV3;

static void
param_init()
{
    uint8_t options = eeprom_read_byte((uint8_t *)Board::kConfigOptions);
    bool should_default = (options & Board::kOptResetConfig);

    // init parameters (set to defaults if requested or not valid)
    for (Parameter::Address addr = Parameter::configBase; addr < Parameter::configTop; addr++) {
        Parameter p(addr);
        uint8_t encoding = param_encoding(addr);

        if (should_default || ((encoding != kEncoding_none) && Encoding::invalid(encoding, p.get()))) {
            p.set(param_default(addr));
        }
    }

    if (should_default) {
        eeprom_update_byte((uint8_t *)Board::kConfigOptions, (options & ~Board::kOptResetConfig));
    }
}

uint8_t
get_assignment(uint8_t output)
{
    const uint16_t assign_base = kParamCH1Assign;
    const uint16_t channel_stride = kParamCH2Assign - kParamCH1Assign;

    return Parameter(assign_base + output * channel_stride).get();
}

uint8_t
get_nad()
{
    return PowerV3::kNodeAddress + Parameter(kParamNodeIndex).get();
}

void
main(void)
{
    Board::early_init();

    // check for recovery mode before constructing anything else
    // v3.x boards, select ID 1, v4.x boards, pull PROG pad low.
    if (Board::get_mode()) {
        Board::panic(Board::kPanicCodeRecovery);
    }

    // construct the slave
    param_init();
    RelaySlave slave(get_nad());
    slave.init();

    // initialise the power switch
    MC17XSF500::configure();

    // enable interrupts
    sei();

    // XXX set up ADC trigger & collection here

    // run the output logic forever
    for (;;) {
        wdt_reset();
        slave.tick();

        // update free memory value each time it's read
        if (free_memory == 0) {
            free_memory = Board::freemem();
        }

        // update outputs - always do this to ensure that any lost update is fixed on
        // the next loop iteration
        for (unsigned output = 0; output < MC17XSF500::num_channels; output++) {

            uint8_t assigned = get_assignment(output);

            if ((assigned != v3_output_assignment::kUnassigned) && slave.test_relay(assigned)) {
                MC17XSF500::set(output, 1);

            } else {
                MC17XSF500::set(output, 0);
            }

            if (!assigned) {
                output_status[output] = v3_output_status::kUnassigned;

            } else {
                // XXX need to use time & knowledge of output type here to be more
                //     intelligent about the state of the load...

                auto status = MC17XSF500::get_status(MC17XSF500::kStatusCH1 + output);

                if (status.chX_status.ots != 0) {
                    output_status[output] = v3_output_status::kTemperatureShutdown;

                } else if (status.chX_status.otw != 0) {
                    output_status[output] = v3_output_status::kTemperatureWarning;

                } else if (status.chX_status.oc_status != 0) {
                    output_status[output] = v3_output_status::kOverCurrent;

                } else if ((status.chX_status.olon != 0) || (status.chX_status.oloff != 0)) {
                    output_status[output] = v3_output_status::kOpenLoad;

                } else {
                    output_status[output] = v3_output_status::kOK;
                }
            }
        }

        // check device status
        auto quick_status = MC17XSF500::get_status(MC17XSF500::kStatusQuick);
        auto device_status = MC17XSF500::get_status(MC17XSF500::kStatusDevice);
        node_status = v3_device_status::kOK;

        info[0] = quick_status.val;
        info[1] = device_status.val;
        info[2] = MC17XSF500::get_status(MC17XSF500::kStatusIO).val;

        // check overload, undervoltage, overvoltage
        if (quick_status.quick_status.ovlf != 0) {
            // prioritise output overload reporting
            node_status = v3_device_status::kOverload;

        } else if (device_status.device_status.uvf != 0) {
            node_status = v3_device_status::kUndervoltage;

        } else if (device_status.device_status.ovf != 0) {
            node_status = v3_device_status::kOvervoltage;
        }
    }
}

void
Parameter::set(uint16_t value) const
{
    switch (address()) {
    case Generic::kParamOperationMode:
        switch (value) {
        case operation_magic::kEnterBootloader:
            Board::enter_bootloader(get_nad(),
                                    board_function::kPowerV3);

        case operation_magic::kSetDefaults:
            Board::reset_to_defaults();
        }

        break;

    case Parameter::configBase ... Parameter::configTop:
        eeprom_update_word((uint16_t *)((address() - Parameter::configBase) * 2), value);
        break;
    }
}

uint16_t
Parameter::get() const
{
    switch (address()) {
    case Generic::kParamProtocolVersion:
        return Master::kNodeProtocolVersion;

    case Generic::kParamBoardFunction:
        return board_function::kPowerV3;

    case Generic::kParamOperationMode:
        return 0;

    case Generic::kParamFirmwareVersion:
        return RELEASE_VERSION;

    case Generic::kParamFirmwarePageSize:
        return SPM_PAGESIZE;

    case Generic::kParamFreeMem: {
        uint16_t temp = free_memory;
        free_memory = 0;
        return temp;
    }

    case Generic::kParamWatchdogResets:
        return Board::wdt_reset_count;

    case kParamDeviceStatus:
        return node_status;

    case kParamCH1Status:
        return output_status[0];

    case kParamCH2Status:
        return output_status[1];

    case kParamCH3Status:
        return output_status[2];

    case kParamCH4Status:
        return output_status[3];

    case kParamCH5Status:
        return output_status[4];

    case kParamCH1Current:
        return current[0];

    case kParamCH2Current:
        return current[1];

    case kParamCH3Current:
        return current[2];

    case kParamCH4Current:
        return current[3];

    case kParamCH5Current:
        return current[4];

    case kParamInfo0 ... kParamInfo7:
        return info[address() - kParamInfo0];

    case Parameter::configBase ... Parameter::configTop:
        return eeprom_read_word((const uint16_t *)((address() - Parameter::configBase) * 2));

    case Parameter::defaultBase ... Parameter::defaultTop:
        return param_default(address() - Parameter::defaultBase + Parameter::configBase);

    }

    return 0;
}

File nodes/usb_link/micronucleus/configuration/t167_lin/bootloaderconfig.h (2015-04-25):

 /* Name: bootloaderconfig.h
 * Micronucleus configuration file. 
 * This file (together with some settings in Makefile.inc) configures the boot loader
 * according to the hardware.
 * 
 * Controller type: ATtiny 167 - 16 MHz with crystal
 * Configuration:   Standard configuration
 *       USB D- :   PB6
 *       USB D+ :   PB3
 *       Entry  :   Always
 *       LED    :   None
 *       OSCCAL :   No change due to external crystal
 * Note: Uses 16 MHz V-USB implementation. 
 * Last Change:     Jul 20,2014
 *
 * License: GNU GPL v2 (see License.txt
 */

#ifndef __bootloaderconfig_h_included__
#define __bootloaderconfig_h_included__

/* ------------------------------------------------------------------------- */
/*                       Hardware configuration.                             */
/*      Change this according to your CPU and USB configuration              */
/* ------------------------------------------------------------------------- */

#define USB_CFG_IOPORTNAME      B
  /* This is the port where the USB bus is connected. When you configure it to
   * "B", the registers PORTB, PINB and DDRB will be used.
   */

#define USB_CFG_DMINUS_BIT      6
/* This is the bit number in USB_CFG_IOPORT where the USB D- line is connected.
 * This may be any bit in the port.
 */
#define USB_CFG_DPLUS_BIT       3
/* This is the bit number in USB_CFG_IOPORT where the USB D+ line is connected.
 * This may be any bit in the port, but must be configured as a pin change interrupt.
 */

#define USB_CFG_CLOCK_KHZ       (F_CPU/1000UL)
/* Clock rate of the AVR in kHz. Legal values are 12000, 12800, 15000, 16000,
 * 16500, 18000 and 20000. The 12.8 MHz and 16.5 MHz versions of the code
 * require no crystal, they tolerate +/- 1% deviation from the nominal
 * frequency. All other rates require a precision of 2000 ppm and thus a
 * crystal!
 * Since F_CPU should be defined to your actual clock rate anyway, you should
 * not need to modify this setting.
 */

/* ------------- Set up interrupt configuration (CPU specific) --------------   */
/* The register names change quite a bit in the ATtiny family. Pay attention    */
/* to the manual. Note that the interrupt flag system is still used even though */
/* interrupts are disabled. So this has to be configured correctly.             */


// setup interrupt for Pin Change for D+

// This is configured for PORTB.

#define USB_INTR_CFG            PCMSK1
#define USB_INTR_CFG_SET        (1 << USB_CFG_DPLUS_BIT)
#define USB_INTR_CFG_CLR        0
#define USB_INTR_ENABLE         PCICR
#define USB_INTR_ENABLE_BIT     PCIE1
#define USB_INTR_PENDING        PCIFR
#define USB_INTR_PENDING_BIT    PCIF1
#define USB_INTR_VECTOR         PCINT1_vect

/* Configuration for PORTA */
/*
#define USB_INTR_CFG            PCMSK0
#define USB_INTR_CFG_SET        (1 << USB_CFG_DPLUS_BIT)
#define USB_INTR_CFG_CLR        0
#define USB_INTR_ENABLE         PCICR
#define USB_INTR_ENABLE_BIT     PCIE0
#define USB_INTR_PENDING        PCIFR
#define USB_INTR_PENDING_BIT    PCIF0
#define USB_INTR_VECTOR         PCINT0_vect
*/

/* ------------------------------------------------------------------------- */
/*       Configuration relevant to the CPU the bootloader is running on      */
/* ------------------------------------------------------------------------- */

// how many milliseconds should host wait till it sends another erase or write?
// needs to be above 4.5 (and a whole integer) as avr freezes for 4.5ms
#define MICRONUCLEUS_WRITE_SLEEP 5


/* ---------------------- feature / code size options ---------------------- */
/*               Configure the behavior of the bootloader here               */
/* ------------------------------------------------------------------------- */
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

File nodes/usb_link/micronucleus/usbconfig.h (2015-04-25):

/* Name: usbconfig.h
 * Project: V-USB, virtual USB port for Atmel's(r) AVR(r) microcontrollers
 * Author: Christian Starkjohann
 * Creation Date: 2005-04-01
 * Tabsize: 4
 * Copyright: (c) 2005 by OBJECTIVE DEVELOPMENT Software GmbH
 * License: GNU GPL v2 (see License.txt), GNU GPL v3 or proprietary (CommercialLicense.txt)
 * This Revision: $Id: usbconfig.h 799 2010-07-27 17:30:13Z cs $
 */

#ifndef __usbconfig_h_included__
#define __usbconfig_h_included__

/* YOU SHOULD NOT NEED TO MODIFY THIS FILE! All configurations are supposed
 * to go into bootloaderconfig.h!
 */

/* ---------------------------- Hardware Config ---------------------------- */

/* All the port and pin assignments, as well as the clock speed and CRC
   setting are now in bootloaderconfig.h: */

#include "bootloaderconfig.h"

/* --------------------------- Functional Range ---------------------------- */

#define USB_CFG_HAVE_INTRIN_ENDPOINT    0
/* Define this to 1 if you want to compile a version with two endpoints: The
 * default control endpoint 0 and an interrupt-in endpoint (any other endpoint
 * number).
 */
#define USB_CFG_HAVE_INTRIN_ENDPOINT3   0
/* Define this to 1 if you want to compile a version with three endpoints: The
 * default control endpoint 0, an interrupt-in endpoint 3 (or the number
 * configured below) and a catch-all default interrupt-in endpoint as above.
 * You must also define USB_CFG_HAVE_INTRIN_ENDPOINT to 1 for this feature.
 */
#define USB_CFG_EP3_NUMBER              3
/* If the so-called endpoint 3 is used, it can now be configured to any other
 * endpoint number (except 0) with this macro. Default if undefined is 3.
 */
/* #define USB_INITIAL_DATATOKEN           USBPID_DATA1 */
/* The above macro defines the startup condition for data toggling on the
 * interrupt/bulk endpoints 1 and 3. Defaults to USBPID_DATA1.
 * Since the token is toggled BEFORE sending any data, the first packet is
 * sent with the oposite value of this configuration!
 */
#define USB_CFG_IMPLEMENT_HALT          0
/* Define this to 1 if you also want to implement the ENDPOINT_HALT feature
 * for endpoint 1 (interrupt endpoint). Although you may not need this feature,
 * it is required by the standard. We have made it a config option because it
 * bloats the code considerably.
 */
#define USB_CFG_SUPPRESS_INTR_CODE      0
/* Define this to 1 if you want to declare interrupt-in endpoints, but don't
 * want to send any data over them. If this macro is defined to 1, functions
 * usbSetInterrupt() and usbSetInterrupt3() are omitted. This is useful if
 * you need the interrupt-in endpoints in order to comply to an interface
 * (e.g. HID), but never want to send any data. This option saves a couple
 * of bytes in flash memory and the transmit buffers in RAM.
 */
#define USB_CFG_INTR_POLL_INTERVAL      10
/* If you compile a version with endpoint 1 (interrupt-in), this is the poll
 * interval. The value is in milliseconds and must not be less than 10 ms for
 * low speed devices.
 */
#ifndef USB_CFG_IS_SELF_POWERED // allow bootloaderconfig.h to override
#define USB_CFG_IS_SELF_POWERED         0
#endif
/* Define this to 1 if the device has its own power supply. Set it to 0 if the
 * device is powered from the USB bus.
 */
#ifndef USB_CFG_MAX_BUS_POWER   // allow bootloaderconfig.h to override
#define USB_CFG_MAX_BUS_POWER           100
#endif
/* Set this variable to the maximum USB bus power consumption of your device.
 * The value is in milliamperes. [It will be divided by two since USB
 * communicates power requirements in units of 2 mA.]
 */
#define USB_CFG_IMPLEMENT_FN_WRITE      0
/* Set this to 1 if you want usbFunctionWrite() to be called for control-out
 * transfers. Set it to 0 if you don't need it and want to save a couple of
 * bytes.
 */
#define USB_CFG_IMPLEMENT_FN_READ       0
/* Set this to 1 if you need to send control replies which are generated
 * "on the fly" when usbFunctionRead() is called. If you only want to send
 * data from a static buffer, set it to 0 and return the data from
 * usbFunctionSetup(). This saves a couple of bytes.
 */
#define USB_CFG_IMPLEMENT_FN_WRITEOUT   0
/* Define this to 1 if you want to use interrupt-out (or bulk out) endpoints.
 * You must implement the function usbFunctionWriteOut() which receives all
 * interrupt/bulk data sent to any endpoint other than 0. The endpoint number
 * can be found in 'usbRxToken'.
 */
#define USB_CFG_HAVE_FLOWCONTROL        0
/* Define this to 1 if you want flowcontrol over USB data. See the definition
 * of the macros usbDisableAllRequests() and usbEnableAllRequests() in
 * usbdrv.h.
 */
#define USB_CFG_DRIVER_FLASH_PAGE       0
/* If the device has more than 64 kBytes of flash, define this to the 64 k page
 * where the driver's constants (descriptors) are located. Or in other words:
 * Define this to 1 for boot loaders on the ATMega128.
 */
#define USB_CFG_LONG_TRANSFERS          0
/* Define this to 1 if you want to send/receive blocks of more than 254 bytes
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

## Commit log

2015-04-02 Implement parameter default access and reset.
    Fixes #117
    Fixes #118
    [main.cpp]
2015-04-04 Update to current sample boards
    [lin_node.brd, lin_node.sch, lin_usb_probe.brd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]
2015-04-04 Remove all references to brake blinking, as it's not a legal behaviour in the USA
2015-04-05 Truth tables for relay behaviour & updated implementation (untested)
2015-04-05 Rewrite truth tables & optimise using k-map tool
    Compiled code is bigger, but overall logic is more manageable and
    source flow is less error-prone.
    Used http://sourceforge.net/projects/truthtablesolve/
2015-04-25 Updates to LINtool and bootloader for the 'real' v1 probe boards
2017-11-12 update master node to v1.1
    [lin_master_node.brd, lin_master_node.sch]
2017-12-20 fix a race condition during inactivity power-down
    It’s possible that LIN traffic could arrive during power-down, causing
    the transceiver to power back up before the controller shuts down. In
    this case, the ms_delay() loop won’t trigger the watchdog, because
    ms_delay() resets the watchdog every millisecond.
    Instead, request power-down just once, and then dead-loop. Either power
    will go away, or the watchdog will fire after ~500ms and the firmware
    will restart.
2019-11-03 Docs for updated 12XS6 series power switches
2019-11-03 soft-programmed node ID for powerv3/v4 boards
2019-11-03 remove defunct dashboard, ecubridge projects
    [controller.brd, controller.sch]

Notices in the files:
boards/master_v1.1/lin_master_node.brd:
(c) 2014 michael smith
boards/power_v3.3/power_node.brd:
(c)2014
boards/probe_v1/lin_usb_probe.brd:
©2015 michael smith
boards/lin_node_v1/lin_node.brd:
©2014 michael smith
